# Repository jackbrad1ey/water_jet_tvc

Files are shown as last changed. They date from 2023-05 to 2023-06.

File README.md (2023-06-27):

Storage and collaboration repository for MEC2402 water jet TVC development.
The purpose of this project was to design and construct a vehicle capable of testing TVC control algorithms. Water is used as its method of propulsion to greatly reduce costs and time during development and ensure safety, allowing for rapid iteration and testing of new control algorithms.

The project features:
- Neptune, a custom flight computer designed to handle communication with ground station, control our servo motors, read from sensors and more.
- Neptune's firmware, consisting of a real time operating system that reads from our sensors and executes instructions based on packets sent from ground station.
- Ground station software, which is used to interact with the vehicle via a Jumper T-lite controller.
- CAD files for the vehicle and the associated testing stand.



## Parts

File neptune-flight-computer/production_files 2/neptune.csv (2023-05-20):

Comment | Designator | Footprint | LCSC
15p | C1,C2 | Capacitor_SMD:C_0805_2012Metric | C1562
10u | C12,C14 | Capacitor_SMD:C_0805_2012Metric_Pad1.18x1.45mm_HandSolder | C440198
1u | C13,C16,C20 | Capacitor_SMD:C_0402_1005Metric
8.2n | C15 | Capacitor_SMD:C_0402_1005Metric | C45186
1n | C17 | Capacitor_SMD:C_0402_1005Metric
10p | C18 | Capacitor_SMD:C_0402_1005Metric
10u | C19 | Capacitor_SMD:C_0603_1608Metric | C19702
10n | C22 | Capacitor_SMD:C_0603_1608Metric
1u | C23 | Capacitor_SMD:C_0603_1608Metric
4.7u | C26 | Capacitor_SMD:C_0603_1608Metric
33p | C3,C21 | Capacitor_SMD:C_0805_2012Metric
100nF | C4,C5,C6,C7,C8,C9,C10,C11,C24,C25 | Capacitor_SMD:C_0603_1608Metric
B5819W | D1,D3 | Diode_SMD:D_SOD-123 | C8598
RB056LAM-40TR | D2 | Diode_SMD:D_SMA | C308719
MountingHole | H1,H2,H3,H4 | MountingHole:MountingHole_3.2mm_M3
THD2528-11SD-GF | J1 | Local Library:THD252811SDGF
Conn_01x02 | J2 | Local Library:XT30PWM
Conn_Coaxial | J3 | Connector_Coaxial:SMA_Amphenol_132291_Vertical
USB_B_Micro | J4 | Connector_USB:USB_Micro-B_Molex-105017-0001
Conn_01x04 | J5,J6,J7 | Connector_PinHeader_2.54mm:PinHeader_1x04_P2.54mm_Vertical
IHLP2020CZER100M01 | L1 | Local Library:IHLP2020CZER100M01 | C844996
10u | L2 | Inductor_SMD:L_0805_2012Metric
Si2301-TP | Q1 | Package_TO_SOT_SMD:SOT-23 | C10487
AO3401A | Q2 | Package_TO_SOT_SMD:SOT-23 | C15127
56k | R1 | Resistor_SMD:R_0402_1005Metric
100k | R2,R5 | Resistor_SMD:R_0402_1005Metric
30k | R3 | Resistor_SMD:R_0402_1005Metric
10k | R4,R10,R11 | Resistor_SMD:R_0402_1005Metric
NC | R6 | Resistor_SMD:R_0402_1005Metric
36.5k | R7 | Resistor_SMD:R_0402_1005Metric | C162860
10.2k | R8 | Resistor_SMD:R_0603_1608Metric | C234238
1.91k | R9 | Resistor_SMD:R_0603_1608Metric | C217858
TS-1187A-B-A-B | SW1,SW2 | Button_Switch_SMD:SW_Push_1P1T_NO_CK_KSC6xxJ | C318884
ADR5040ARTZ-2.048 | U1 | Package_TO_SOT_SMD:SOT-23 | C144273
LM393 | U2 | Local Library:SOIC127P600X175-8N | C7955
TPS54331D | U3 | Package_SO:SOIC-8-1EP_3.9x4.9mm_P1.27mm_EP2.29x3mm_ThermalVias | C9865
LP3993-33B3F | U4 | Package_TO_SOT_SMD:SOT-23 | C387705
RFM95W-915S2 | U5 | RF_Module:HOPERF_RFM9XW_SMD
USBLC6-2SC6 | U6 | Package_TO_SOT_SMD:SOT-23-6 | C2827654
STM32F411RETx | U7 | Package_QFP:LQFP-64_10x10mm_P0.5mm | C94355
BMX055 | U8 | Local Library:BMX055
32.768k | Y1 | Crystal:Crystal_SMD_3215-2Pin_3.2x1.5mm | C620155
12MHz | Y2 | Crystal:Crystal_SMD_5032-4Pin_5.0x3.2mm

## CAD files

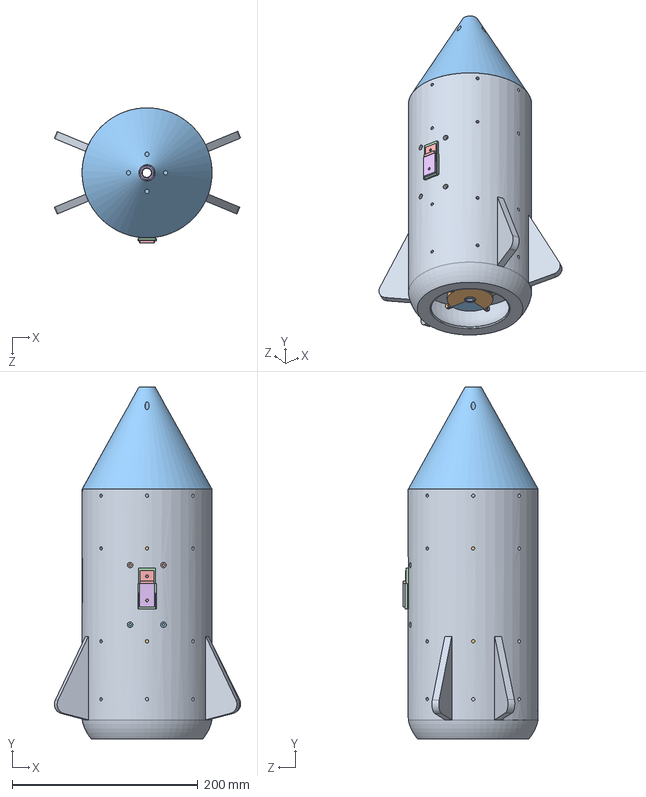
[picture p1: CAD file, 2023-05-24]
CAD/Vehicle_assembly.SLDASM
200.7 x 379.0 x 145.8 mm
Bodytube
2nozzleservorodmount - pt1
2nozzleservorodmount - pt2
v3-ballheadjoint x 2
v2-ballattatchemnet x 4
rods x 2
v3-ballheadjoint - servoside x 2
servo x 2
tvcbulkhead
Bottom half tube
Battery casing
PCB
Battery casing upper
Nozzle connection
nozzle-Pipe adapter
PVC pipe
step push fitting
Upper connection
nosecone
cable puller (sticks out less)
hinge placeholder
door

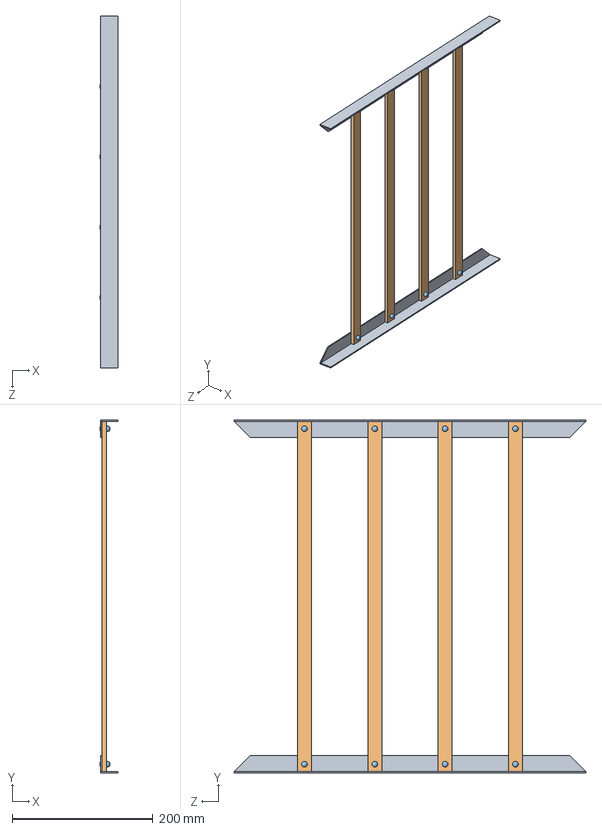
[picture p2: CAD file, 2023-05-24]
CAD/Cage/Roof.SLDASM
26.2 x 502.0 x 500.0 mm
right_angle x 2
Halfbar(roof) x 4
4mm rivet x 8

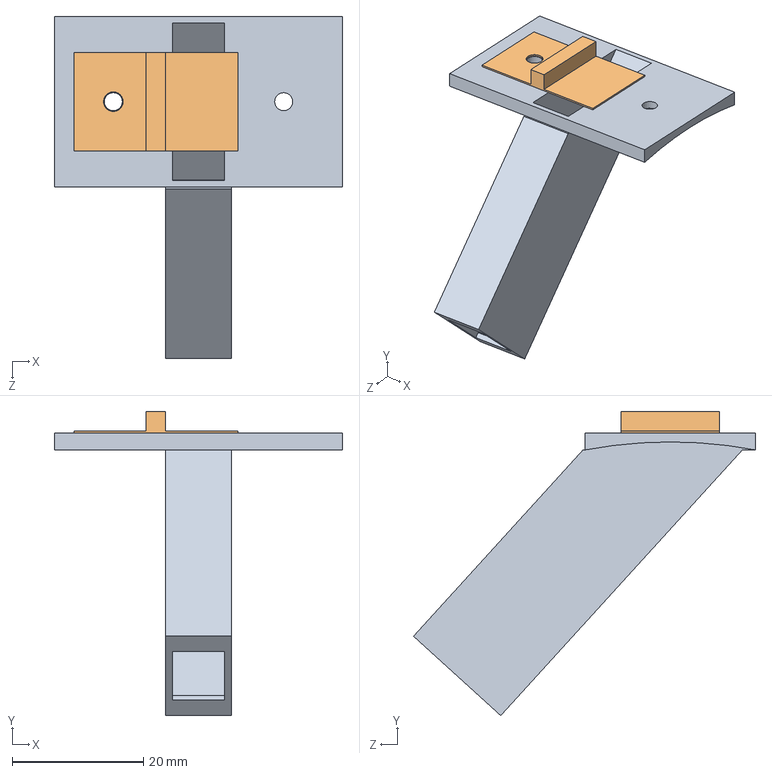
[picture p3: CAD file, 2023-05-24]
CAD/Sensor stack/puller.SLDASM
44.0 x 46.4 x 52.2 mm
cable puller (sticks out less)
hinge placeholder

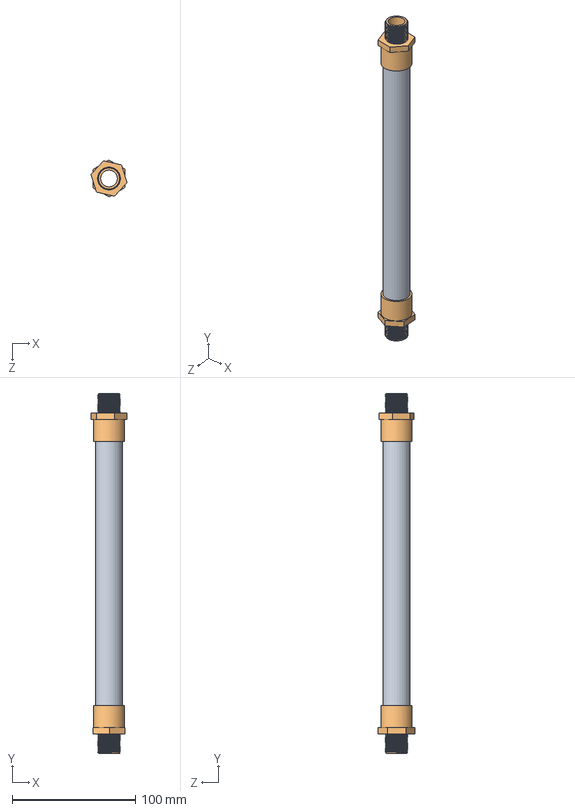
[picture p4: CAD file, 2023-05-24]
CAD/Water Delivery/Plenum pipe assem.SLDASM
29.3 x 292.0 x 30.0 mm
PVC pipe_2.0
0.5_inch_male x 2

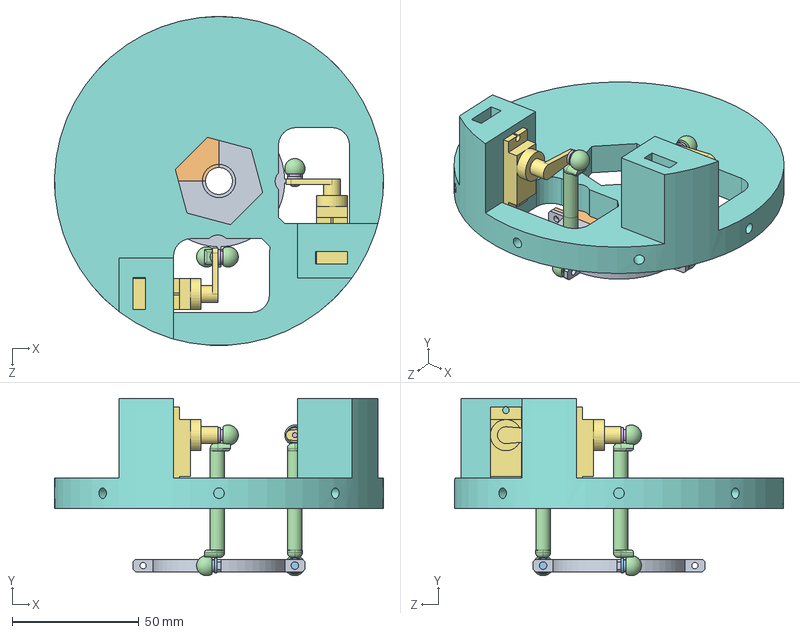
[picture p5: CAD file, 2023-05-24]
CAD/TVC/tvc_assem.SLDASM
130.0 x 70.1 x 130.0 mm
2nozzleservorodmount - pt1
2nozzleservorodmount - pt2
v3-ballheadjoint x 2
v2-ballattatchemnet x 4
rods x 2
v3-ballheadjoint - servoside x 2
servo x 2
tvcbulkhead

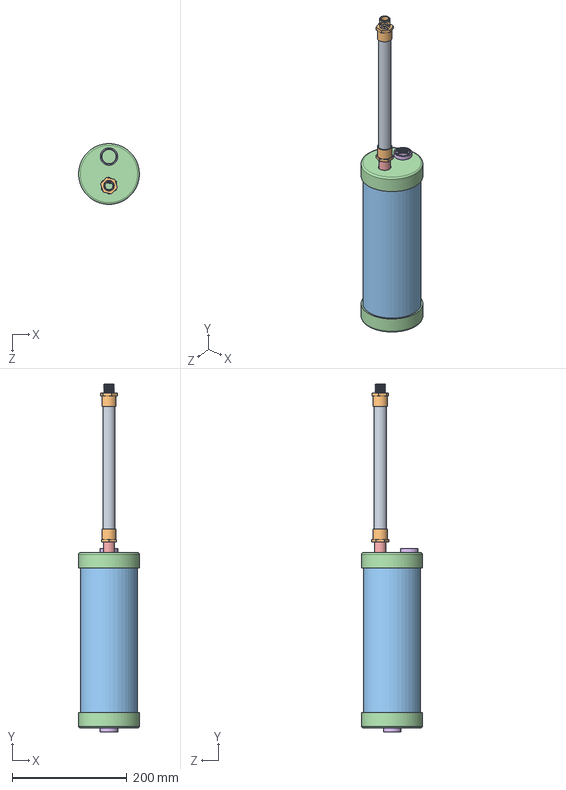
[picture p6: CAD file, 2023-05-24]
CAD/Water Delivery/Plenum full assem.SLDASM
106.0 x 607.0 x 106.0 mm
PVC pipe_2.0
0.5_inch_male x 2
Plenum_pipe
plenum_end_cap x 2
0.5_inch_female
female_3.4_inch x 2

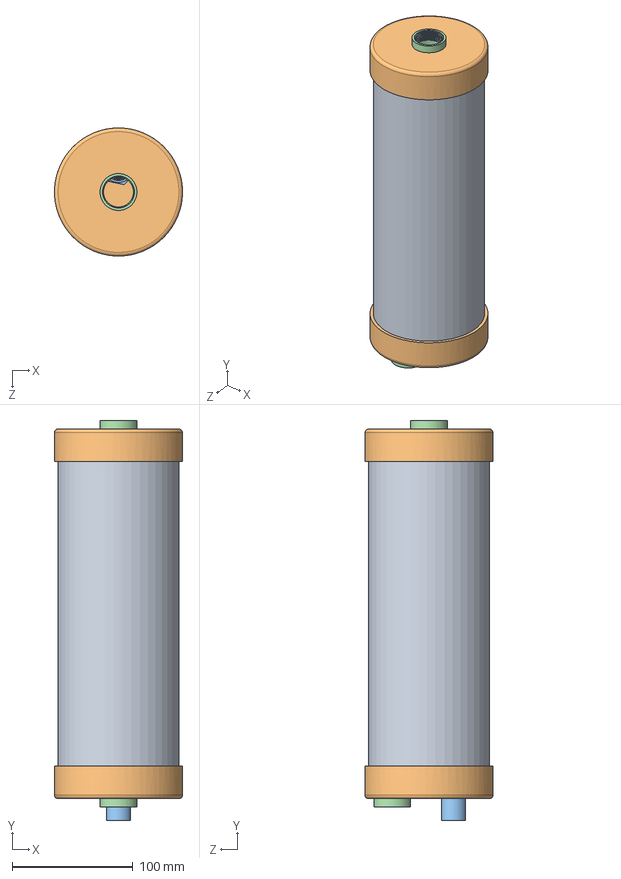
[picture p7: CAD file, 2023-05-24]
CAD/Water Delivery/plenum.SLDASM
106.0 x 331.0 x 106.0 mm
Plenum_pipe
plenum_end_cap x 2
0.5_inch_female
female_3.4_inch x 2

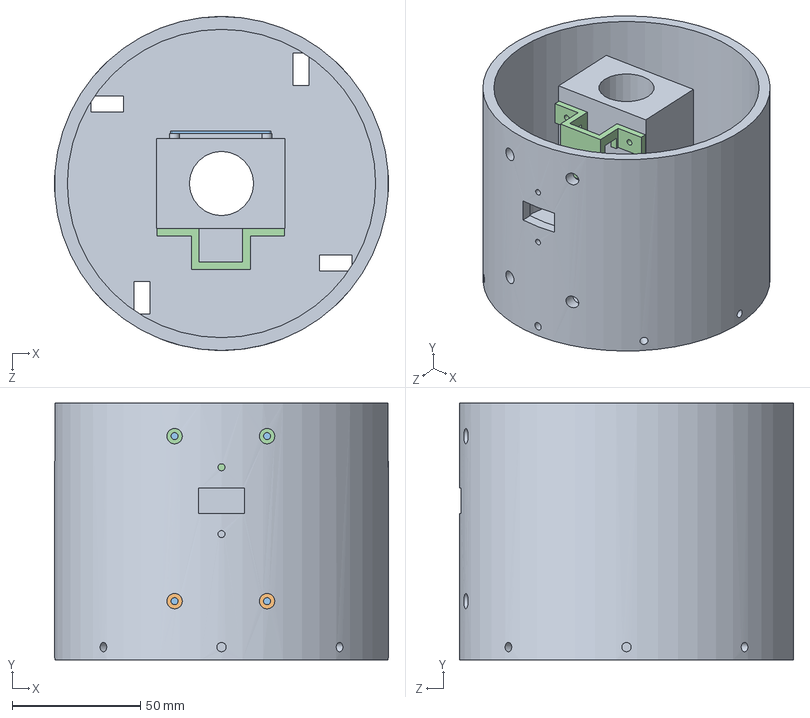
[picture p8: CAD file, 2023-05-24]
CAD/Sensor stack/sensor stack assem.SLDASM
130.0 x 100.0 x 130.0 mm
Bottom half tube
Battery casing
PCB
Battery casing upper

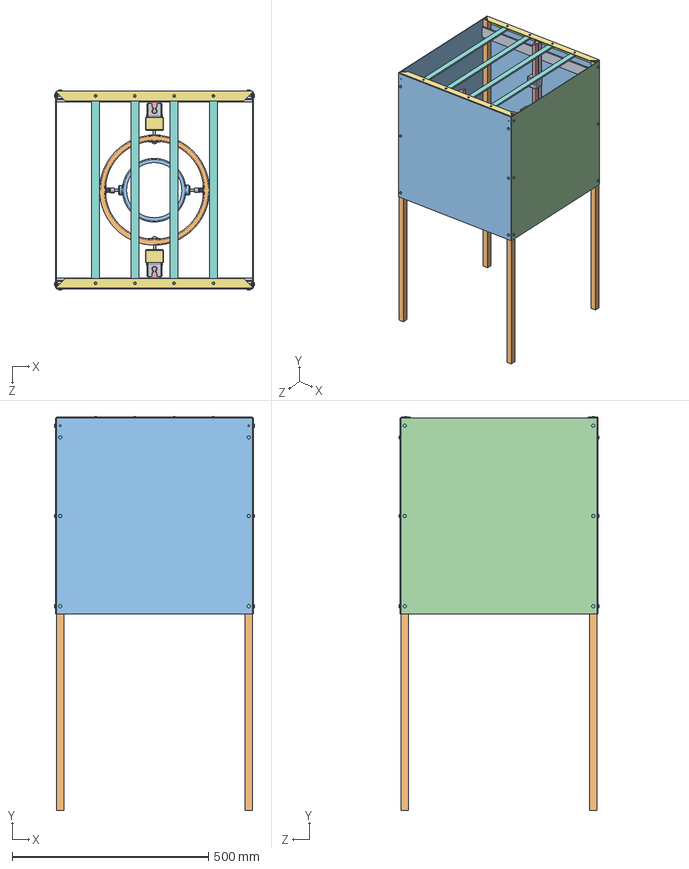
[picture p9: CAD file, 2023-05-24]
CAD/Cage/Cage.SLDASM
510.0 x 1003.2 x 510.0 mm
Bar x 4
RotationRing
InnerRotationMount
BoltSquare x 4
22x8x7 bearing x 4
RingHardstop x 2
right_angle x 2
Halfbar(roof) x 4
4mm rivet x 8
SHS x 4
Polycarbonate Sheet x 3
Plywood Sheet
SBR12 Linear Rail x 2
SBR12UU x 2
SBR12UU Mount x 2
m5 bolt_unthreaded x 24
Hardstop x 4

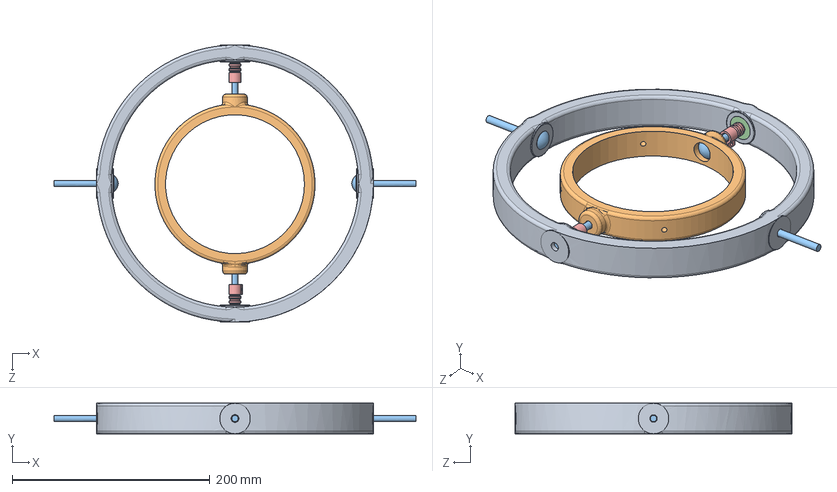
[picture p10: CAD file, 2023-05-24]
CAD/Cage/CageAssembly.SLDASM
366.0 x 31.0 x 280.0 mm
RotationRing
InnerRotationMount
BoltSquare x 4
22x8x7 bearing x 2
RingHardstop x 2

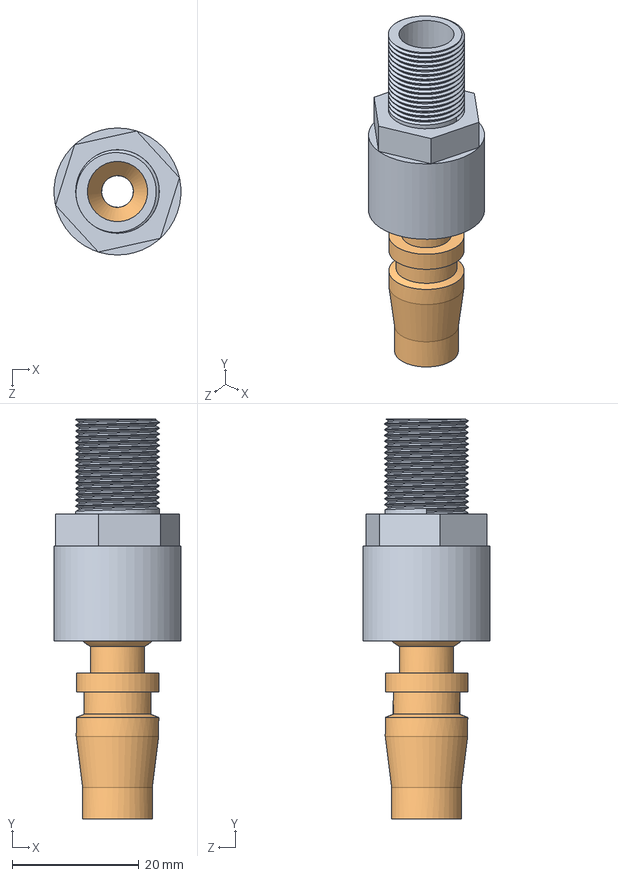
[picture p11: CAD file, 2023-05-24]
CAD/Water Delivery/Nozzle.SLDASM
20.0 x 63.0 x 20.0 mm
Nozzle top
NozzleTip

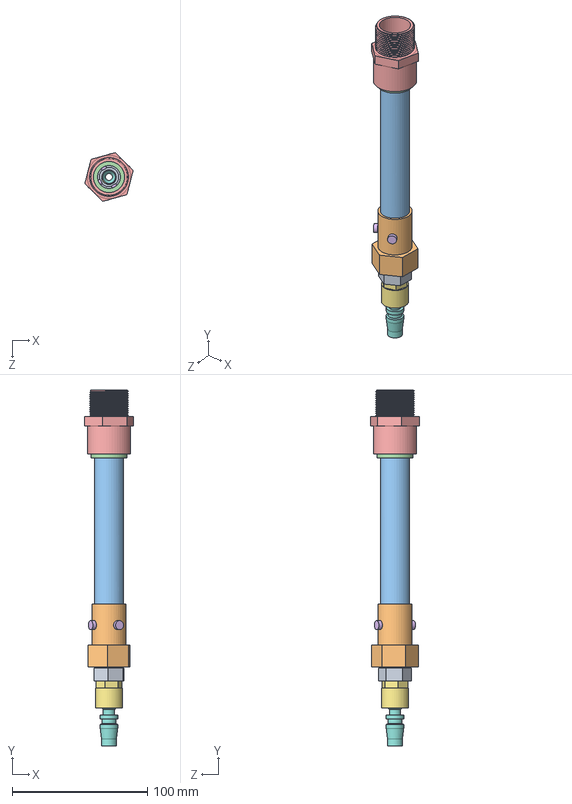
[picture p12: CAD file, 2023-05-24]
CAD/Water Delivery/Water Delivery.SLDASM
35.9 x 263.0 x 36.0 mm
Poly Threaded Bushing
Press faucet Socket
PVC pipe
Reducing Bushing
Press valve Socket
M4x6 bolt x 3
Nozzle top
NozzleTip

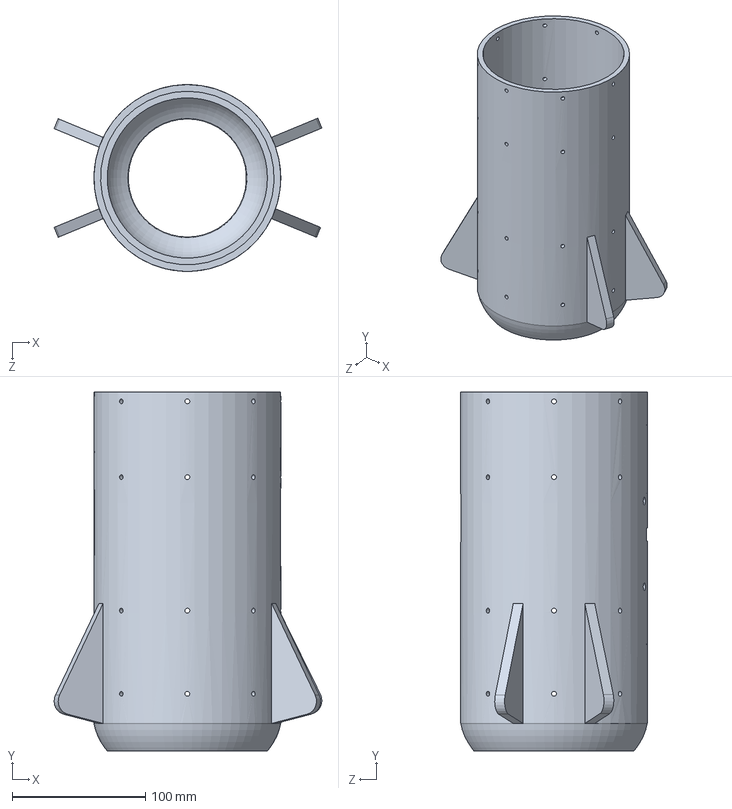
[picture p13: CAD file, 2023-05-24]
CAD/BODY/Bodytube.SLDPRT
200.7 x 269.0 x 140.0 mm

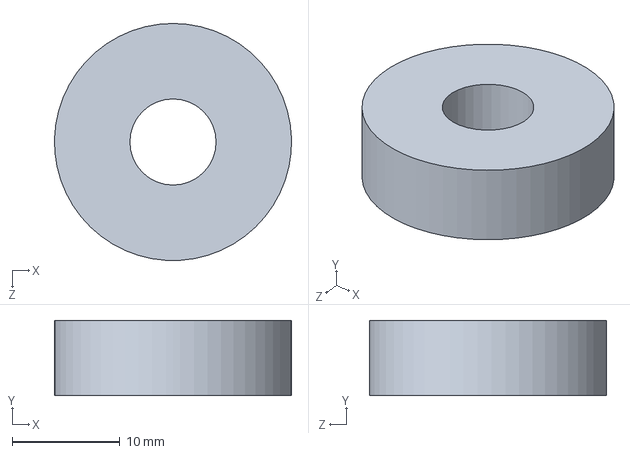
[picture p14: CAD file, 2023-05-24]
CAD/Cage/22x8x7 bearing.SLDPRT
22.0 x 7.00 x 22.0 mm

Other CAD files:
CAD/Sensor stack/PCB.SLDPRT
CAD/TVC/STLs/tvcbulkhead3.STL
CAD/TVC/v3-ballheadjoint - servoside.SLDPRT
CAD/BODY/nosecone.SLDPRT
CAD/BODY/STLs/Bodytube.STL
CAD/BODY/STLs/nosecone.STL
CAD/Cage/4.x.x/4.1.x/4.1.1.SLDDRW
CAD/Cage/4.x.x/4.1.x/4.1.2.SLDDRW
CAD/Cage/4.x.x/4.1.x/4.1.3.SLDDRW
CAD/Cage/4.x.x/4.1.x/4.1.4.SLDDRW
CAD/Cage/4.x.x/4.1.x/4.1.5.SLDDRW
CAD/Cage/4.x.x/4.1.x/4.1.6.SLDDRW
CAD/Cage/4.x.x/4.2.x/4.2.0.SLDDRW
CAD/Cage/4.x.x/4.2.x/4.2.1.SLDDRW
CAD/Cage/4.x.x/4.2.x/4.2.2.SLDDRW
CAD/Cage/4.x.x/4.2.x/4.2.3.SLDDRW
CAD/Cage/4.x.x/4.3.x/4.3.0.SLDDRW
CAD/Cage/4.x.x/4.3.x/4.3.1.SLDDRW
CAD/Cage/4.x.x/4.3.x/4.3.2.SLDDRW
CAD/Cage/4mm rivet.SLDPRT
CAD/Cage/Bar.SLDPRT
CAD/Cage/BoltSquare.SLDPRT
CAD/Cage/Halfbar(roof).SLDPRT
CAD/Cage/Hardstop.SLDPRT
CAD/Cage/InnerRotationMount.SLDPRT
CAD/Cage/Plywood Sheet.SLDPRT
CAD/Cage/Polycarbonate Sheet.SLDPRT
CAD/Cage/RingHardstop.SLDPRT
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

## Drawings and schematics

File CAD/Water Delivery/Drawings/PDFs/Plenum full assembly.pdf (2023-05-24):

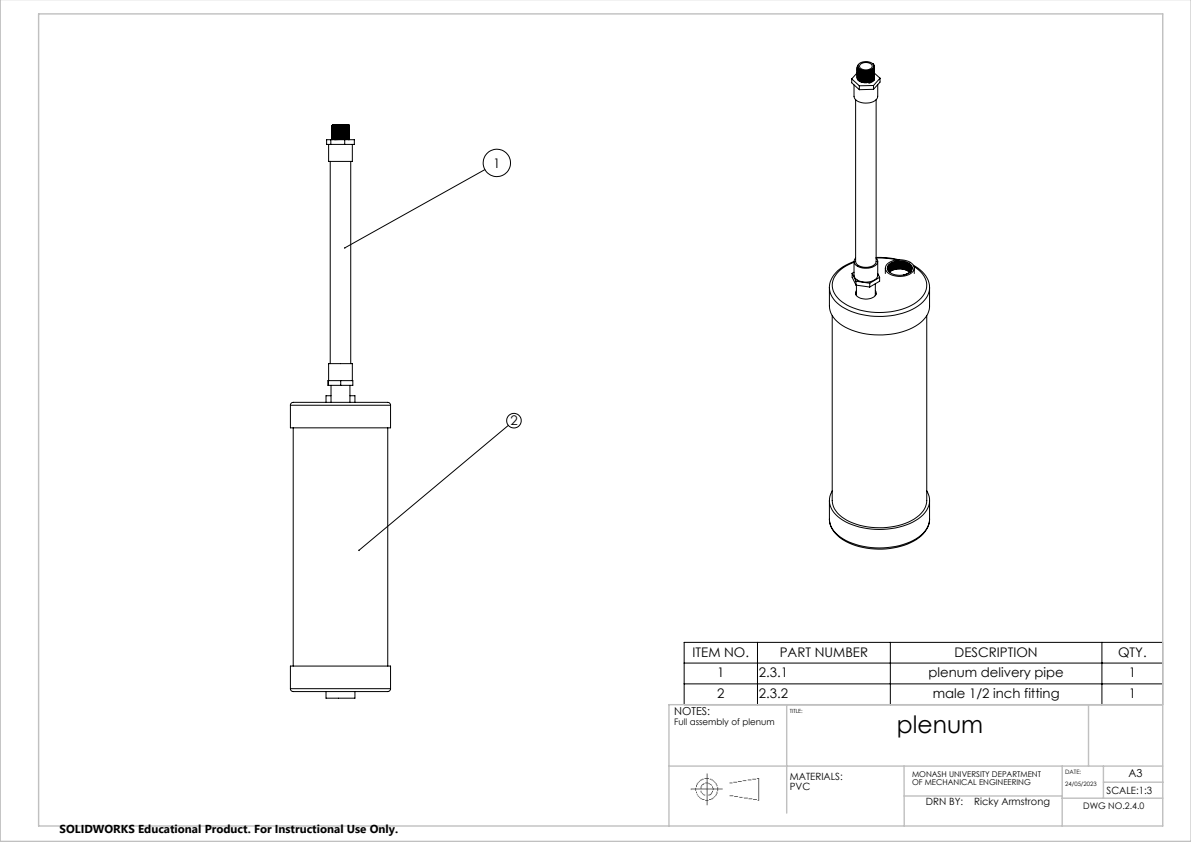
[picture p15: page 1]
DWG NO.2.4.0

ITEM NO. | PART NUMBER | DESCRIPTION | QTY.
1 | 2.3.1 | plenum delivery pipe | 1
2 | 2.3.2 | male 1/2 inch fitting | 1
NOTES: Full assembly of plenum | TITLE: plenum

MONASH UNIVERSITY DEPARTMENT OF MECHANICAL ENGINEERING | DATE: 24/05/2023 | A3

DRN BY: Ricky Armstrong

SOLIDWORKS Educational Product. For Instructional Use Only.

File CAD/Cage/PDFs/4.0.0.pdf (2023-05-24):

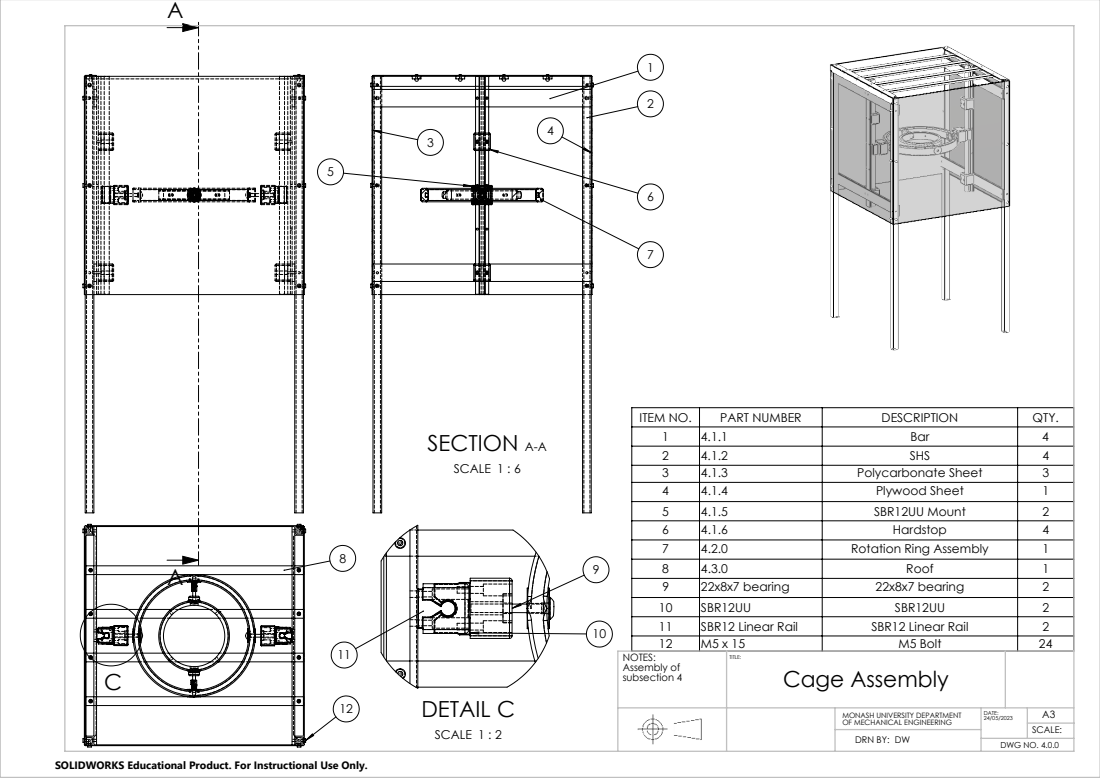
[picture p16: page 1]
SECTION A-A; SCALE 1 : 6; DETAIL C; SCALE 1 : 2; ITEM NO.; PART NUMBER; DESCRIPTION; QTY.; Polycarbonate Sheet; Plywood Sheet; SBR12UU Mount; Rotation Ring Assembly; 22x8x7 bearing; SBR12 Linear Rail; M5 Bolt; DWG NO. 4.0.0; Cage Assembly; Assembly of subsection 4

MONASH UNIVERSITY DEPARTMENT
OF MECHANICAL ENGINEERING
DRN BY: DW

SOLIDWORKS Educational Product. For Instructional Use Only.

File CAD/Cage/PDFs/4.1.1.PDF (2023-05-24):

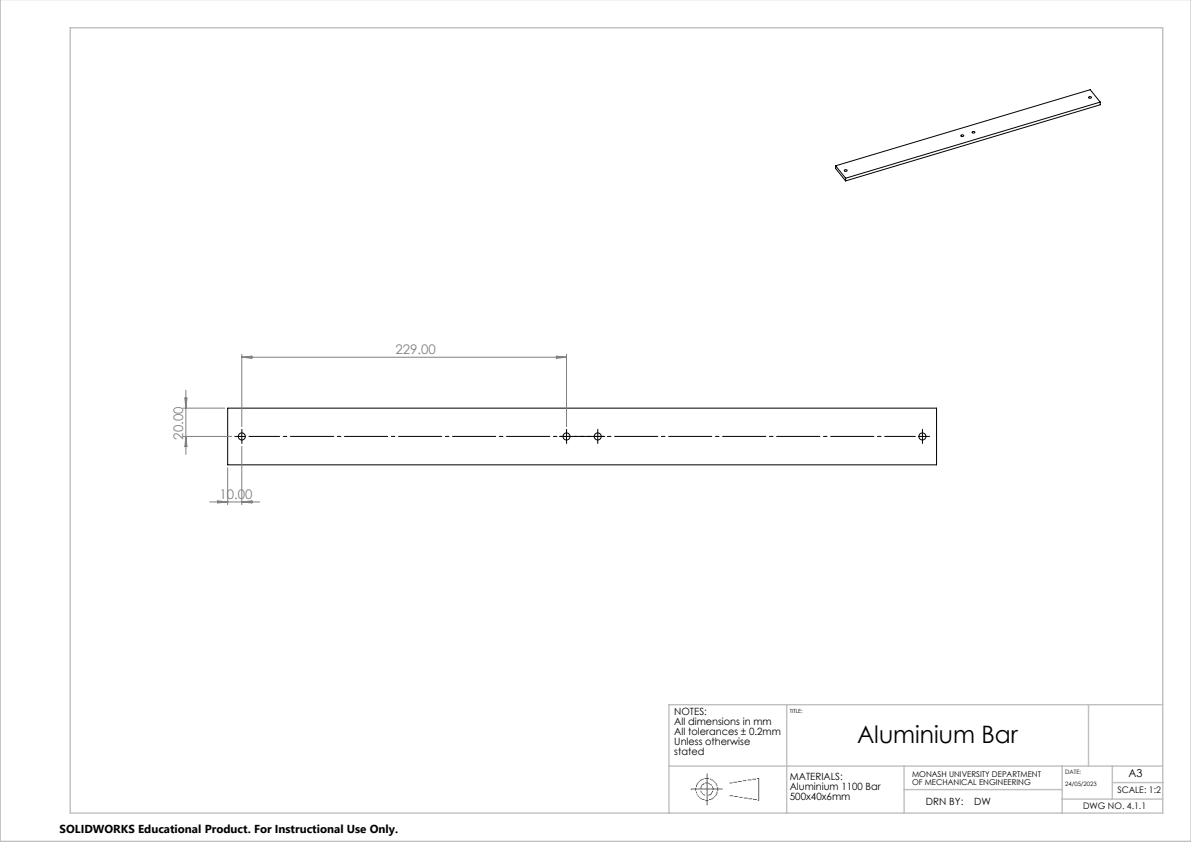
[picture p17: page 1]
DWG NO. 4.1.1; SCALE: 1:2

NOTES: All dimensions in mm All tolerances ± 0.2mm Unless otherwise stated | TITLE: Aluminium Bar

MATERIALS: Aluminium 1100 Bar 500x40x6mm | MONASH UNIVERSITY DEPARTMENT OF MECHANICAL ENGINEERING | DATE: 24/05/2023 | A3

DRN BY: DW

SOLIDWORKS Educational Product. For Instructional Use Only.

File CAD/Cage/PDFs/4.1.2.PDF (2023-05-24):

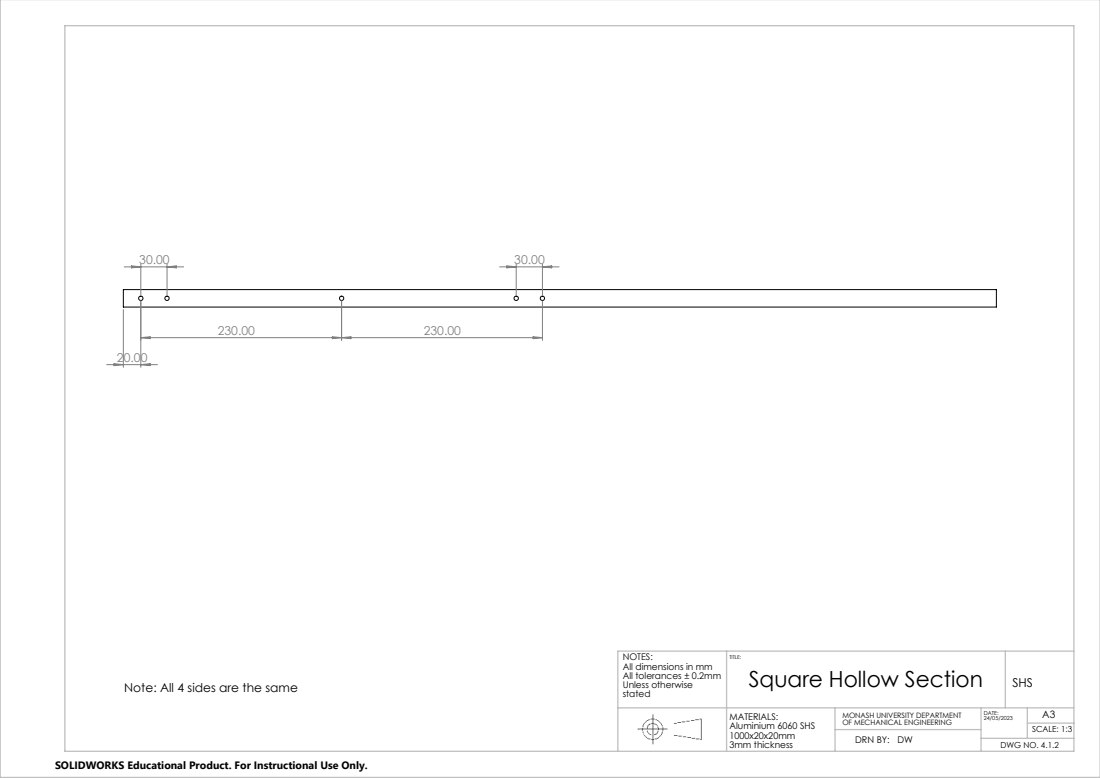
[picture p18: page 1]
DWG NO. 4.1.2; SCALE: 1:3

NOTES: All dimensions in mm All tolerances ± 0.2mm Unless otherwise stated | TITLE: Square Hollow Section | SHS

Note: All 4 sides are the same

MATERIALS: Aluminium 6060 SHS 1000x20x20mm 3mm thickness | MONASH UNIVERSITY DEPARTMENT OF MECHANICAL ENGINEERING | DATE: 24/05/2023 | A3

DRN BY: DW

SOLIDWORKS Educational Product. For Instructional Use Only.

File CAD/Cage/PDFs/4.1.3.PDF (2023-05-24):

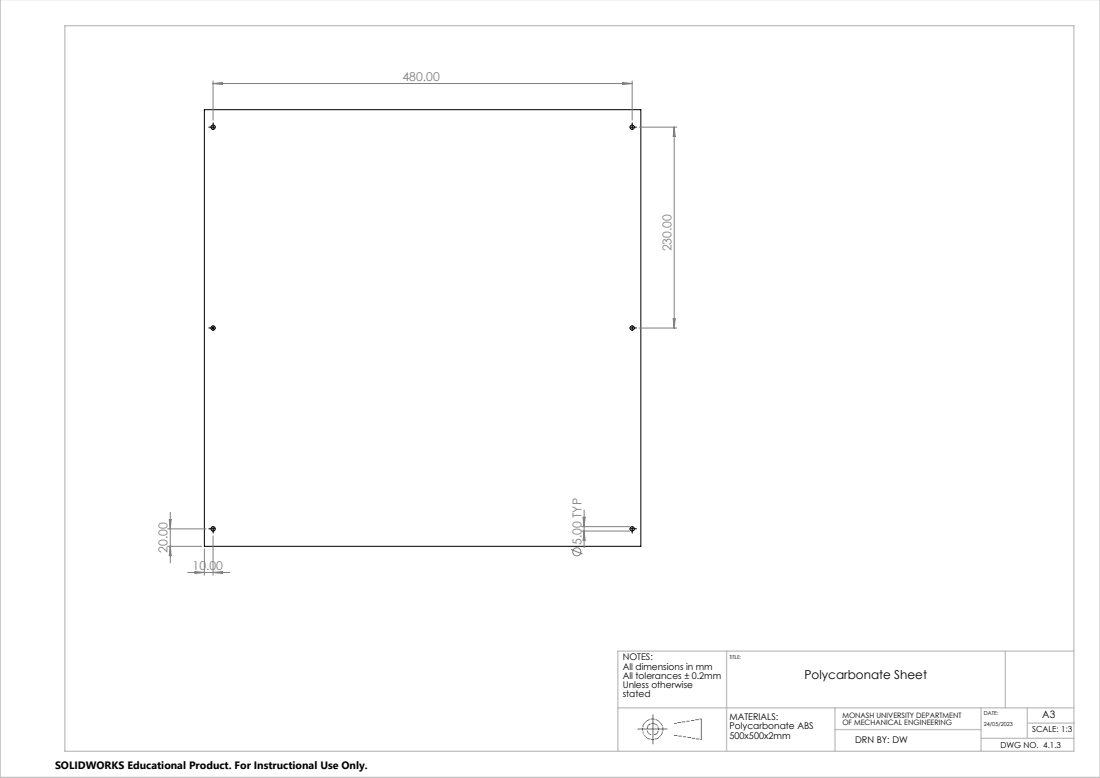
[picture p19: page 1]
5.00 TYP; DWG NO. 4.1.3; SCALE: 1:3

NOTES: All dimensions in mm All tolerances ± 0.2mm Unless otherwise stated | TITLE: Polycarbonate Sheet

MATERIALS: Polycarbonate ABS 500x500x2mm | MONASH UNIVERSITY DEPARTMENT OF MECHANICAL ENGINEERING | DATE: 24/05/2023 | A3

DRN BY: DW

SOLIDWORKS Educational Product. For Instructional Use Only.

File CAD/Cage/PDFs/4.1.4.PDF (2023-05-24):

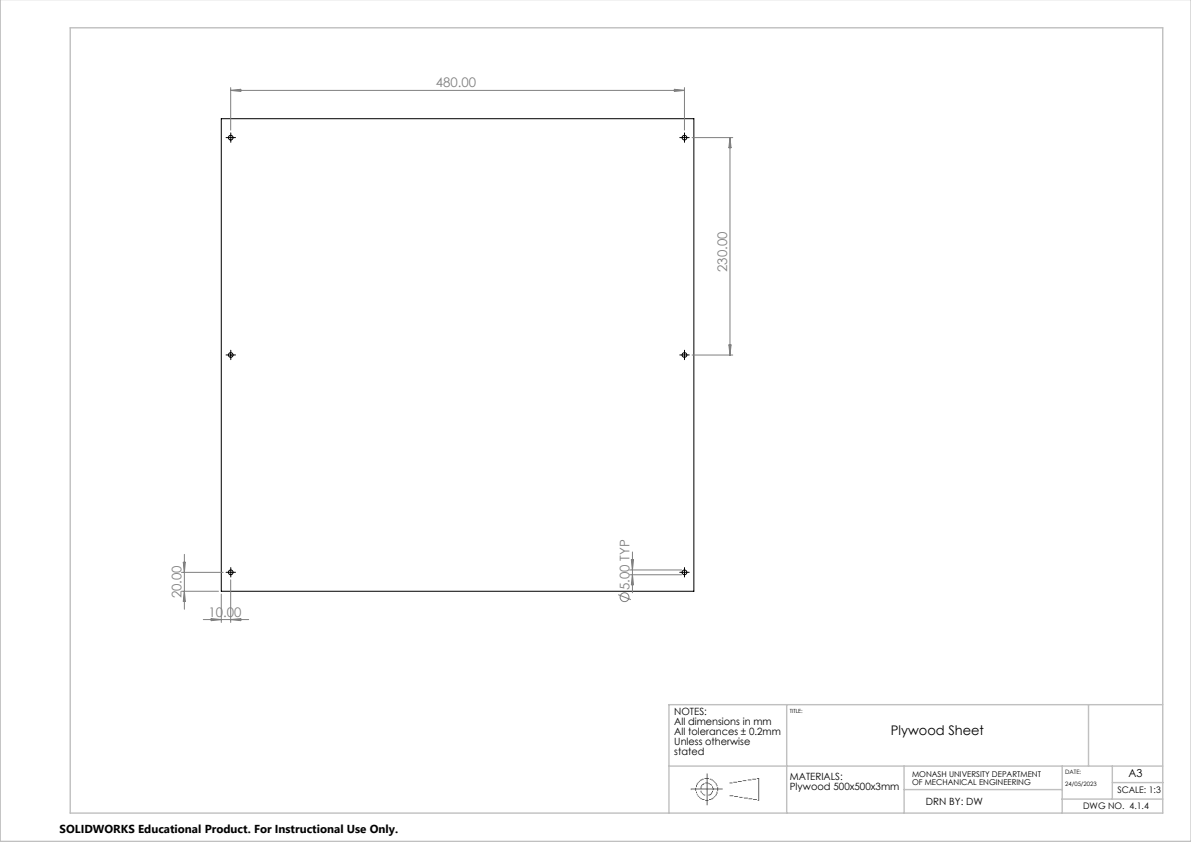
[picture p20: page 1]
5.00 TYP; DWG NO. 4.1.4; SCALE: 1:3

NOTES: All dimensions in mm All tolerances ± 0.2mm Unless otherwise stated | TITLE: Plywood Sheet

MATERIALS: Plywood 500x500x3mm | MONASH UNIVERSITY DEPARTMENT OF MECHANICAL ENGINEERING | DATE: 24/05/2023 | A3

DRN BY: DW

SOLIDWORKS Educational Product. For Instructional Use Only.

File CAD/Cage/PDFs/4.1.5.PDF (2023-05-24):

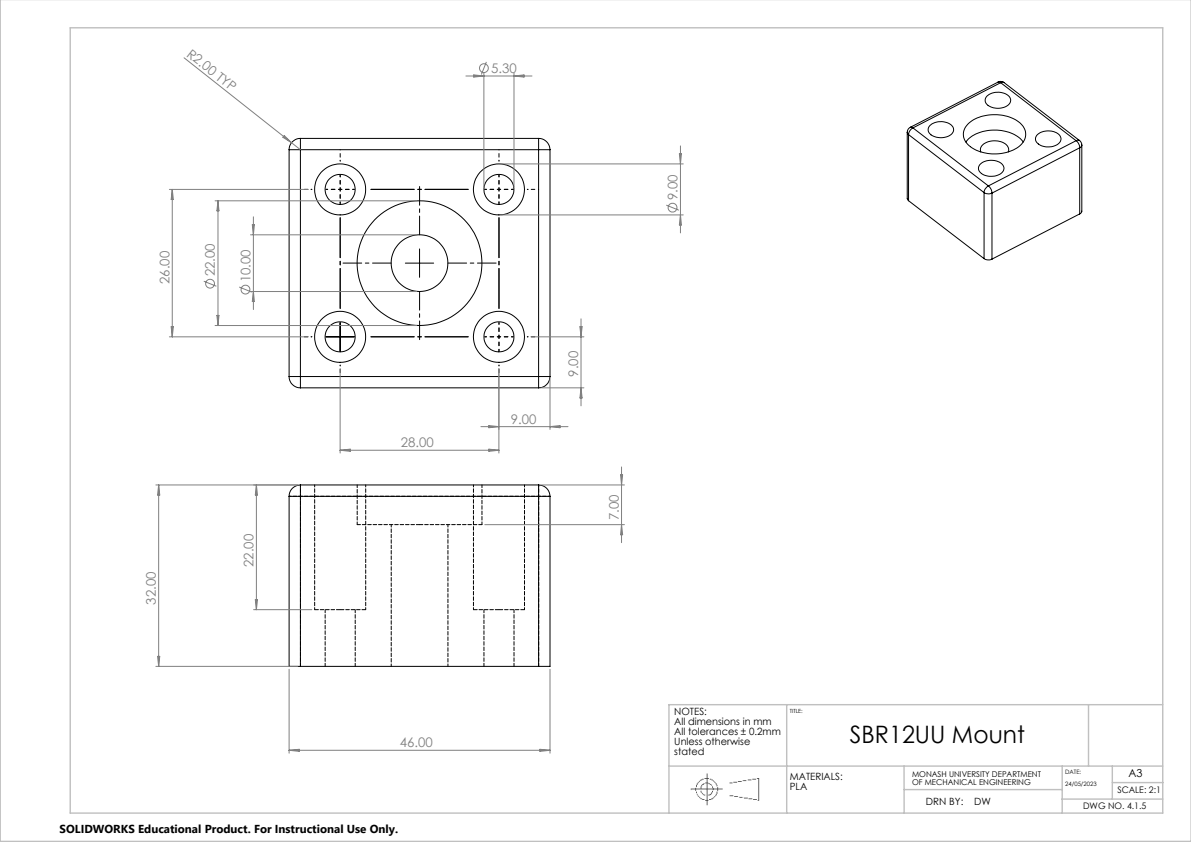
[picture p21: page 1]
R2.00 TYP; DWG NO. 4.1.5; SCALE: 2:1

NOTES: All dimensions in mm All tolerances ± 0.2mm Unless otherwise stated | TITLE: SBR12UU Mount

MATERIALS: PLA | MONASH UNIVERSITY DEPARTMENT OF MECHANICAL ENGINEERING | DATE: 24/05/2023 | A3

DRN BY: DW

SOLIDWORKS Educational Product. For Instructional Use Only.

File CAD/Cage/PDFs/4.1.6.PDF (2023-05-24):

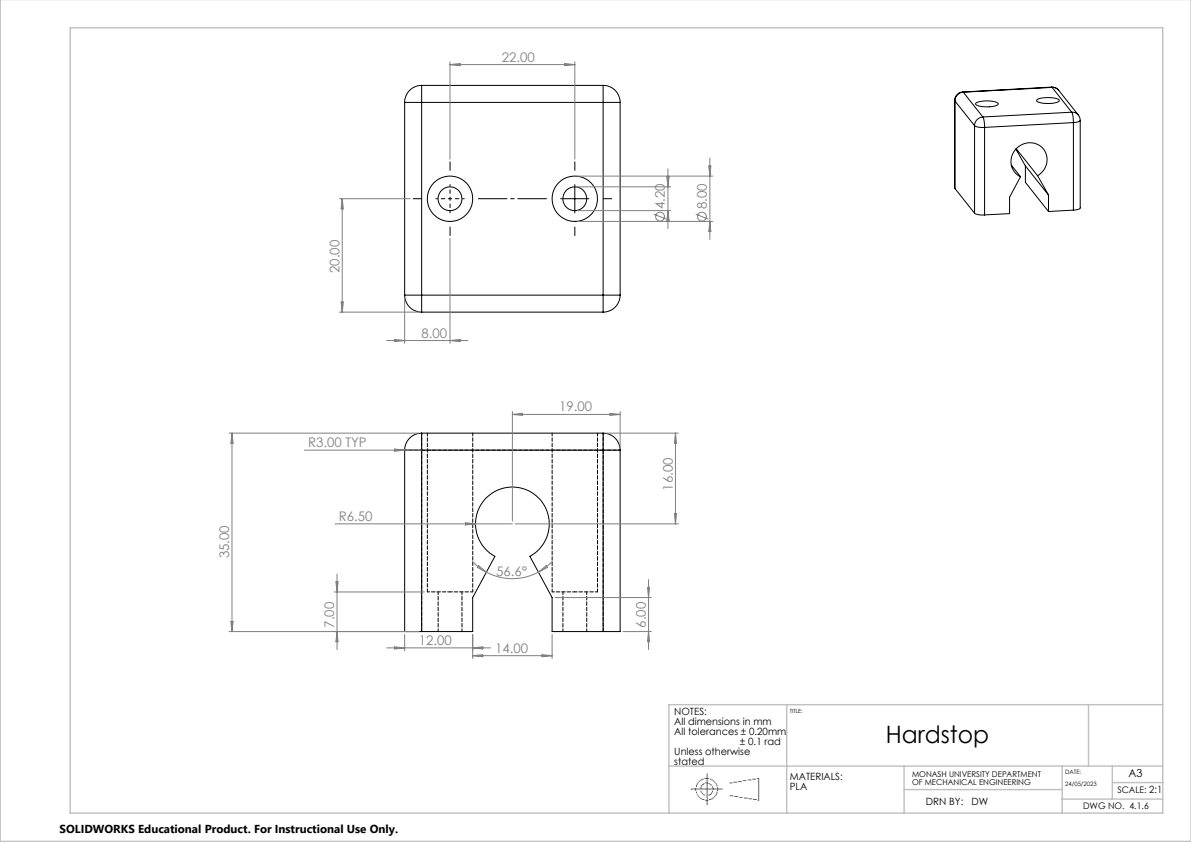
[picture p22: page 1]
R3.00 TYP; DWG NO. 4.1.6; SCALE: 2:1

NOTES: All dimensions in mm All tolerances ± 0.20mm ± 0.1 rad Unless otherwise stated | TITLE: Hardstop

MATERIALS: PLA | MONASH UNIVERSITY DEPARTMENT OF MECHANICAL ENGINEERING | DATE: 24/05/2023 | A3

DRN BY: DW

SOLIDWORKS Educational Product. For Instructional Use Only.

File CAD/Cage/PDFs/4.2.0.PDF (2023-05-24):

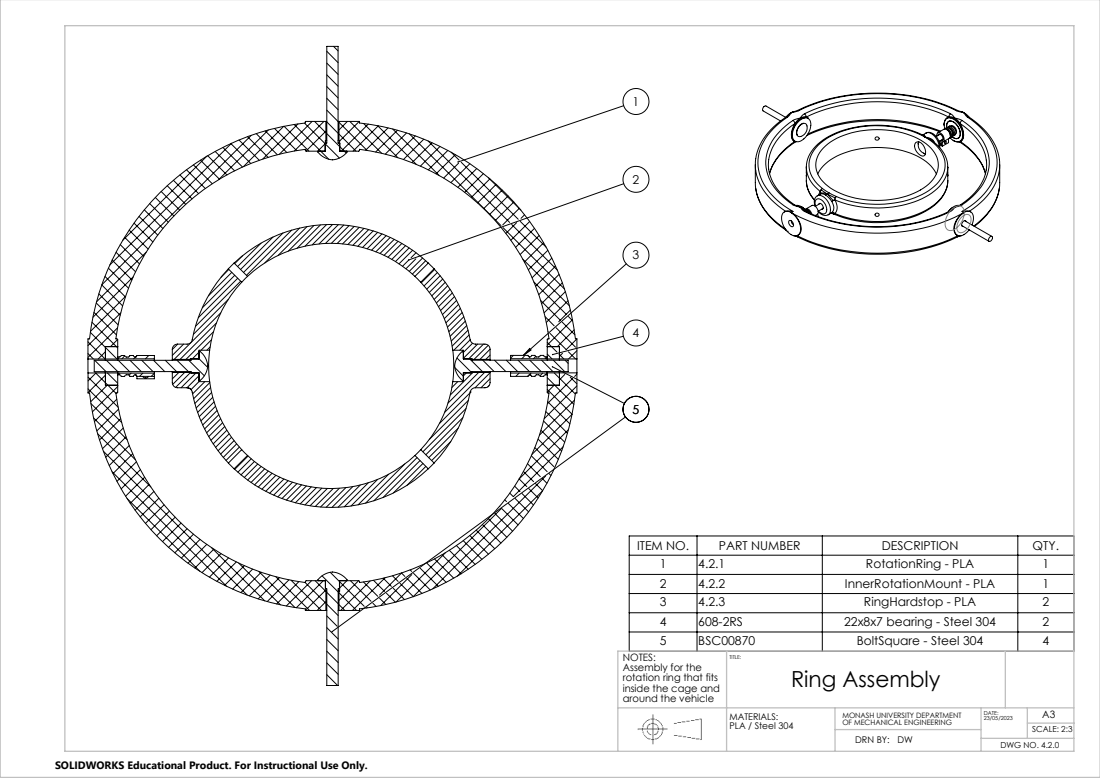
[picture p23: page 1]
DWG NO. 4.2.0; SCALE: 2:3

ITEM NO. | PART NUMBER | DESCRIPTION | QTY.
1 | 4.2.1 | RotationRing - PLA | 1
2 | 4.2.2 | InnerRotationMount - PLA | 1
3 | 4.2.3 | RingHardstop - PLA | 2
4 | 608-2RS | 22x8x7 bearing - Steel 304 | 2
5 | BSC00870 | BoltSquare - Steel 304 | 4
NOTES: Assembly for the rotation ring that fits inside the cage and around the vehicle | TITLE: Ring Assembly

MATERIALS: PLA / Steel 304 | MONASH UNIVERSITY DEPARTMENT OF MECHANICAL ENGINEERING | DATE: 23/05/2023 | A3

DRN BY: DW

SOLIDWORKS Educational Product. For Instructional Use Only.

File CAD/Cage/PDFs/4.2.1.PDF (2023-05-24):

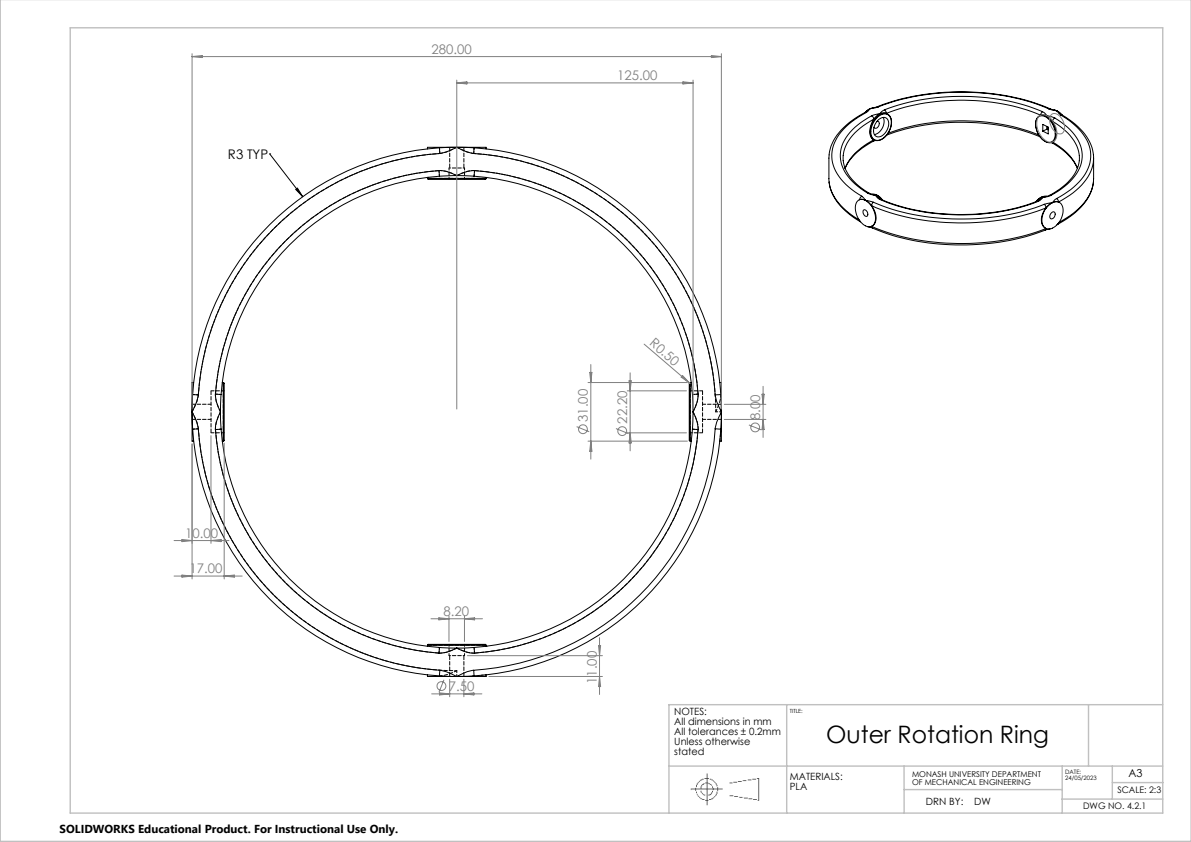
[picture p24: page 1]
R3 TYP; DWG NO. 4.2.1; SCALE: 2:3

NOTES: All dimensions in mm All tolerances ± 0.2mm Unless otherwise stated | TITLE: Outer Rotation Ring

MATERIALS: PLA | MONASH UNIVERSITY DEPARTMENT OF MECHANICAL ENGINEERING | DATE: 24/05/2023 | A3

DRN BY: DW

SOLIDWORKS Educational Product. For Instructional Use Only.

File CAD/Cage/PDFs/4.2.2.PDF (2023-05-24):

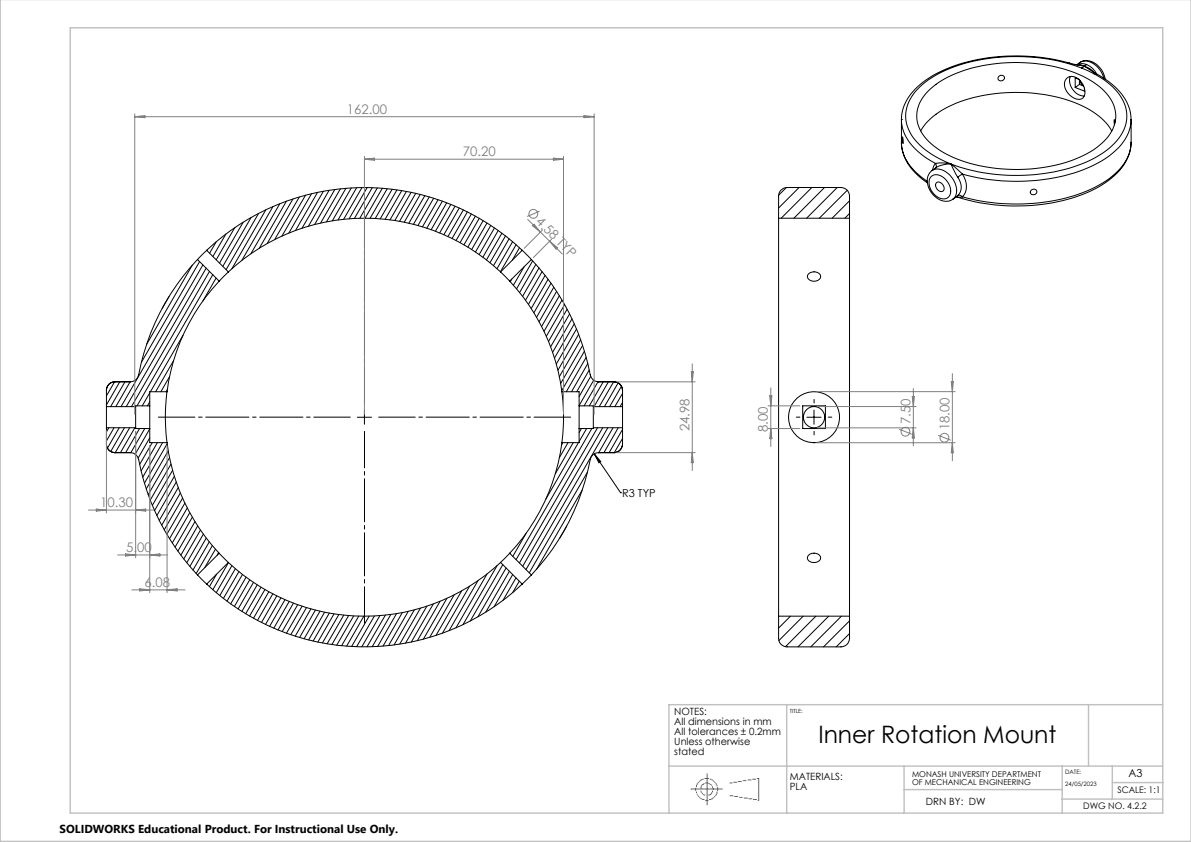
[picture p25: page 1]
4.58 TYP; R3 TYP; DWG NO. 4.2.2; SCALE: 1:1

NOTES: All dimensions in mm All tolerances ± 0.2mm Unless otherwise stated | TITLE: Inner Rotation Mount

MATERIALS: PLA | MONASH UNIVERSITY DEPARTMENT OF MECHANICAL ENGINEERING | DATE: 24/05/2023 | A3

DRN BY: DW

SOLIDWORKS Educational Product. For Instructional Use Only.

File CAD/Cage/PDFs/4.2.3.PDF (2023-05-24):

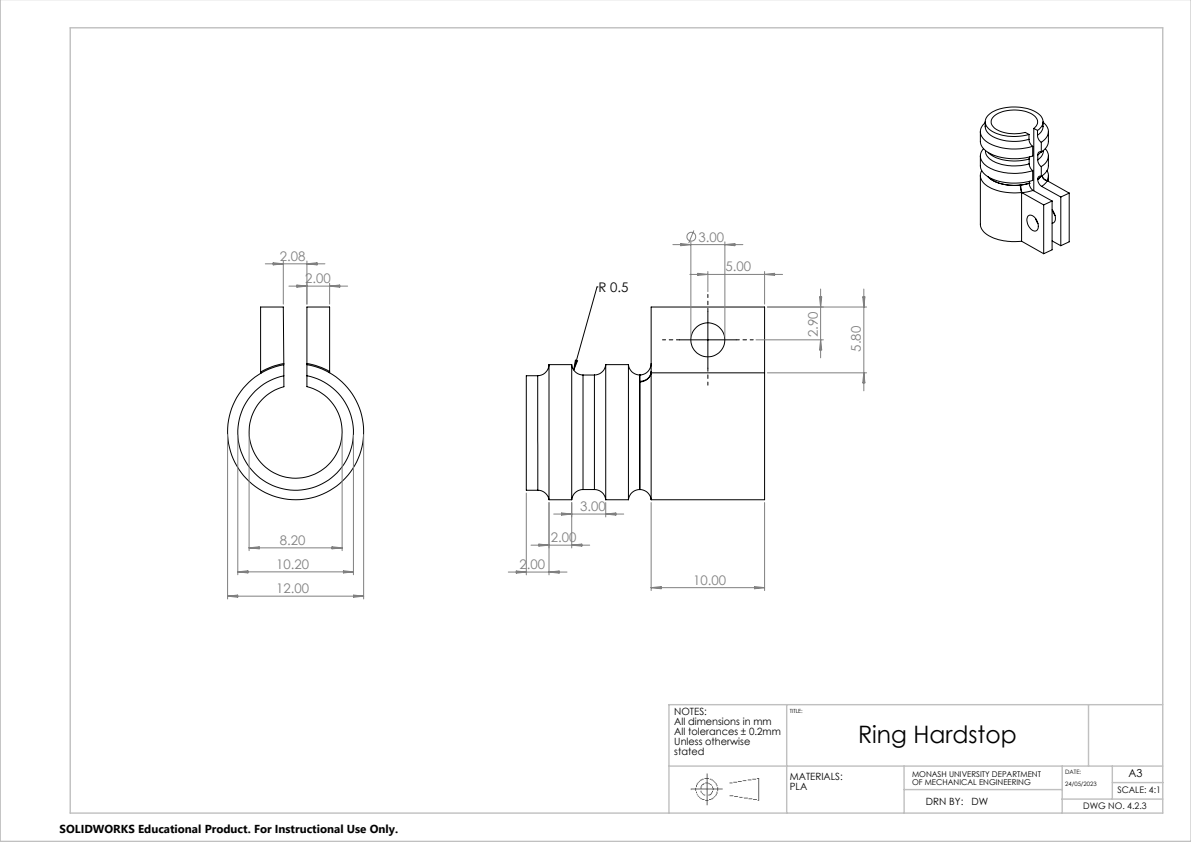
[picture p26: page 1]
DWG NO. 4.2.3; SCALE: 4:1

NOTES: All dimensions in mm All tolerances ± 0.2mm Unless otherwise stated | TITLE: Ring Hardstop

MATERIALS: PLA | MONASH UNIVERSITY DEPARTMENT OF MECHANICAL ENGINEERING | DATE: 24/05/2023 | A3

DRN BY: DW

SOLIDWORKS Educational Product. For Instructional Use Only.

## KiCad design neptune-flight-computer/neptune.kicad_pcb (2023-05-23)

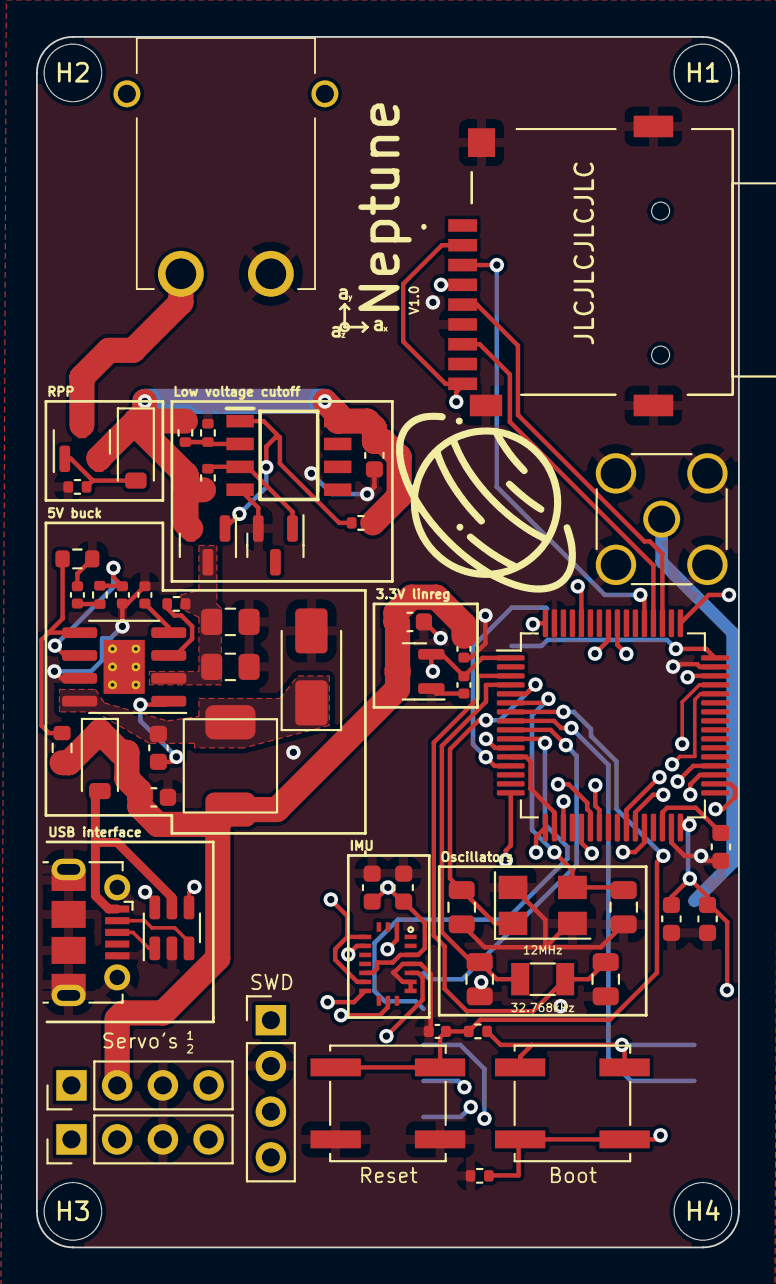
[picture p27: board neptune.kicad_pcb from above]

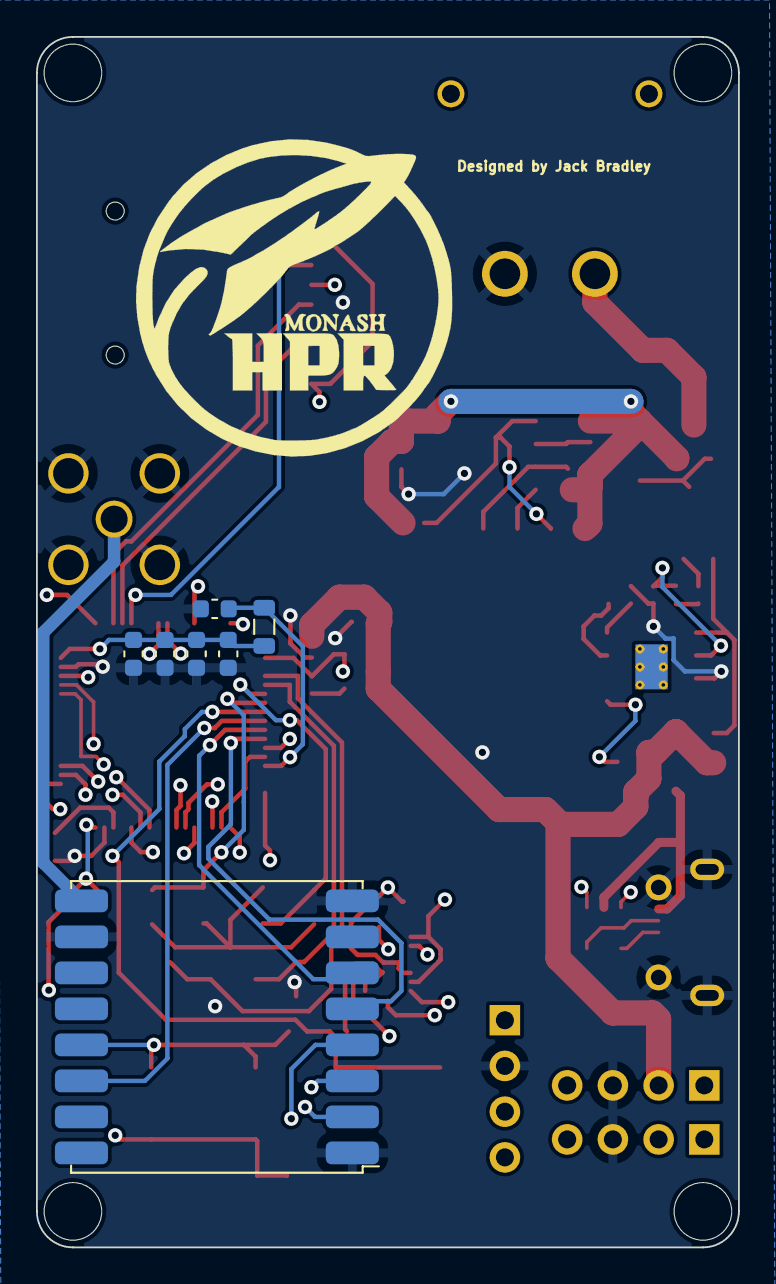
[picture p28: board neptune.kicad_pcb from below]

Board: 4 copper layers, 39.0 x 67.2 mm, 68 parts (8 on the bottom side), 54 nets.

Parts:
C1, C2: 15p; C_0805_2012Metric
C3, C21: 33p; C_0805_2012Metric
C4, C5, C6, C7, C8, C9, C10, C11, C24, C25: 100nF; C_0603_1608Metric
C12, C14: 10u; C_0805_2012Metric_Pad1.18x1.45mm_HandSolder
C13, C16, C20: 1u; C_0402_1005Metric
C15: 8.2n; C_0402_1005Metric
C17: 1n; C_0402_1005Metric
C18: 10p; C_0402_1005Metric
C19: 10u; C_0603_1608Metric
C22: 10n; C_0603_1608Metric
C23: 1u; C_0603_1608Metric
C26: 4.7u; C_0603_1608Metric
D1, D3: B5819W; D_SOD-123
D2: RB056LAM-40TR; D_SMA
H1, H2, H3, H4: MountingHole; MountingHole_3.2mm_M3
H5: HPR_Logo
J1: THD2528-11SD-GF; THD252811SDGF
J2: Conn_01x02; XT30PWM
J3: Conn_Coaxial; SMA_Amphenol_132291_Vertical
J4: USB_B_Micro; USB_Micro-B_Molex-105017-0001
J5, J6, J7: Conn_01x04; PinHeader_1x04_P2.54mm_Vertical
L1: IHLP2020CZER100M01
L2: 10u; L_0805_2012Metric
Q1: Si2301-TP; SOT-23
Q2: AO3401A; SOT-23
R1, R4: 30k; R_0402_1005Metric
R2, R5: 100k; R_0402_1005Metric
R3: 56k; R_0402_1005Metric
R6: NC; R_0402_1005Metric
R7: 36.5k; R_0402_1005Metric
R8: 10.2k; R_0603_1608Metric
R9: 1.91k; R_0603_1608Metric
R10, R11: 10k; R_0402_1005Metric
SW1, SW2: TS-1187A-B-A-B; SW_Push_1P1T_NO_CK_KSC6xxJ
U1: ADR5040ARTZ-2.048; SOT-23
U2: LM393; SOIC127P600X175-8N
U3: TPS54331D; SOIC-8-1EP_3.9x4.9mm_P1.27mm_EP2.29x3mm_ThermalVias
U4: LP3993-33B3F; SOT-23
U5: RFM95W-915S2; HOPERF_RFM9XW_SMD
U6: USBLC6-2SC6; SOT-23-6
U7: STM32F411RETx; LQFP-64_10x10mm_P0.5mm
U8: BMX055
Y1: 32.768k; Crystal_SMD_3215-2Pin_3.2x1.5mm
Y2: 12MHz; Crystal_SMD_5032-4Pin_5.0x3.2mm

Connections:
+3.3V: C4.1, C5.1, C16.1, J1.4 (VDD), U4.2 (VOUT), U5.13 (3.3V)
+3V3: C9.1, C10.1, C22.1, C23.1, C24.1, C25.1, J5.1, L2.1, R11.2, SW1.2, U7.1 (VBAT), U7.19 (VDD), U7.32 (VDD), U7.48 (VDD), U7.64 (VDD), U8.3 (VDD), U8.13 (VDDIO)
+5V: C6.1, C13.1, C19.1, D3.1 (K), J6.2, J7.2, L1.2, R8.2, U4.3 (VIN)
/CE_ACC: U7.26 (PB0), U8.16 (CSB1)
/CE_GYR: U7.27 (PB1), U8.5 (CSB2)
/CE_MAG: U7.28 (PB2), U8.20 (CSB3)
/CLK_SD: J1.5 (CLX), U7.51 (PC10)
/CS_RF: U5.5 (NSS), U7.10 (PC2)
/CS_SD: J1.2 (CD/DAT3), J1.9 (CD), U7.11 (PC3)
/IMU_MISO: U7.22 (PA6), U8.12 (SDO2), U8.17 (SDO1)
/IMU_MOSI: U7.23 (PA7), U8.11 (SDX)
/IMU_SCK: U7.21 (PA5), U8.9 (SCX)
/MISO_RF: U5.2 (MISO), U7.35 (PB14)
/MISO_SD: J1.7 (DAT0), U7.52 (PC11)
/MOSI_RF: U5.3 (MOSI), U7.36 (PB15)
/MOSI_SD: J1.3 (CMD), U7.53 (PC12)
/RESET_RF: U5.6 (RESET), U7.9 (PC1)
/RF_1O0: U5.14 (DIO0), U7.8 (PC0)
/SCK_RF: U5.4 (SCK), U7.34 (PB13)
/STM32/BOOT0: R10.2, SW1.1, U7.60 (BOOT0)
/STM32/NRST: C20.1, R11.1, SW2.2, U7.7 (NRST)
/STM32/OSC32_IN: C1.1, U7.3 (PC14), Y1.1
/STM32/OSC32_OUT: C2.1, U7.4 (PC15), Y1.2
/STM32/OSC_IN: C21.1, U7.5 (PH0), Y2.1
/STM32/OSC_OUT: C3.1, U7.6 (PH1), Y2.3
/STM32/S1_control: J6.1, U7.56 (PB4)
/STM32/S1_feedback: J6.4, U7.16 (PA2)
/STM32/S2_control: J7.1, U7.57 (PB5)
/STM32/S2_feedback: J7.4, U7.17 (PA3)
/STM32/SWCLK: J5.4, U7.49 (PA14)
/STM32/SWDIO: J5.3, U7.46 (PA13)
/STM32/USB_D+: U6.6 (I/O1), U7.45 (PA12)
/STM32/USB_D-: U6.4 (I/O2), U7.44 (PA11)
/STM32/USB_conn_D+: J4.3 (D+), U6.1 (I/O1)
/STM32/USB_conn_D-: J4.2 (D-), U6.3 (I/O2)
GND: C1.2, C2.2, C3.2, C4.2, C5.2, C6.2, C7.2, C9.2, C10.2, C11.2, C12.2, C13.2, C14.2, C15.2, C16.2, C17.2, C18.2, C19.2, C20.2, C21.2, C22.2, C23.2, C24.2, C25.2, C26.2, D2.2 (A), J1.6 (VSS), J1.MP1, J1.MP2, J1.MP3, J1.MP4, J2.2, J3.2 (Ext), J4.5 (GND), J4.6 (Shield), J5.2, J6.3, J7.3, R2.1, R4.1, R9.1, R10.1, SW2.1, U1.2 (A), U2.4 (V-), U3.7 (GND), U4.1 (GND), U5.1 (GND), U5.8 (GND), U5.10 (GND), U6.2 (GND), U7.12 (VSSA), U7.18 (VSS), U7.31 (VSS), U7.47 (VSS), U7.63 (VSS), U8.4 (GNDA), U8.6 (GNDIO), U8.7 (PS), Y2.2, Y2.4
unnamed: C17.1, R7.1
unnamed: D1.2 (A), Q1.1 (G), R2.2
unnamed: C8.2, D2.1 (K), L1.1, U3.8 (PH)
unnamed: J2.1, Q1.3 (D)
unnamed: J3.1 (In), U5.9 (ANT)
unnamed: Q2.1 (G), R5.1, U2.1
unnamed: R1.1, U1.1 (K), U2.3 (+)
unnamed: R3.1, R4.2, U2.2 (-)
unnamed: C8.1, U3.1 (BOOT)
unnamed: C18.1, R7.2, U3.6 (COMP)
unnamed: R6.1, U3.3 (EN)
unnamed: C15.1, U3.4 (SS)
unnamed: R8.1, R9.2, U3.5 (VSENSE)
unnamed: C26.1, U7.30 (VCAP1)
unnamed: C11.1, L2.2, U7.13 (VDDA)
VBUS: D3.2 (A), J4.1 (VBUS), U6.5 (VBUS)
VCC: C12.1, C14.1, Q2.3 (D), R6.2, U3.2 (VIN)
VDC: C7.1, D1.1 (K), Q1.2 (S), Q2.2 (S), R1.2, R3.2, R5.2, U2.8 (V+)

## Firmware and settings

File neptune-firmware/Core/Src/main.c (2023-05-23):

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
/* Includes ------------------------------------------------------------------*/
#include "main.h"
#include "cmsis_os.h"
#include "usb_device.h"

/* USER CODE BEGIN Includes */
#include <math.h>
#include <string.h>
#include "usbd_cdc_if.h"
#include "arm_math.h"

#include "BMX055.h"
#include "LoRa.h"
#include "Sensors.h"
#include "packets.h"
#include "EKF.h"
#include "utils.h"
#include "servos.h"

// #include "arm_math.h"
// #include "usbd_cdc_if.h"
// #include "string.h"
// #include "BMX055.h"
// #include "Sensors.h"
// #include "utils.h"
// #include "packets.h"
// #include "LoRa.h"
// #include "servos.h"
// #include "EKF.h"

// #include <stdbool.h>
// #include <math.h>
// #include "usbd_cdc_if.h"
// #include "arm_math.h"

// #include "BMX055.h"
// #include "MS5611.h"
// #include "LoRa.h"
// #include "Sensors.h"
// #include "Packets.h"
// #include "EKF.h"
// #include "debug.h"
// #include "gps.h"
// #include "State_Machine.h"
/* USER CODE END Includes */

/* USER CODE BEGIN PTD */
#define SAMPLE_FREQUENCY 100
#define ACCEL_ALPHA 0.9
#define GYRO_ALPHA 0.5
/* USER CODE END PTD */

/* USER CODE BEGIN PD */
float32_t hard_iron_offset_data[3] = { 46.5, 74.0, -44.0 };
float32_t soft_iron_offset_data[9] = { 1, 0, 0, 0, 1, 0, 0, 0, 1 };
/* USER CODE END PD */

ADC_HandleTypeDef hadc1;

SPI_HandleTypeDef hspi1;
SPI_HandleTypeDef hspi2;
SPI_HandleTypeDef hspi3;

TIM_HandleTypeDef htim2;
TIM_HandleTypeDef htim3;

/* Definitions for SensorRead */
osThreadId_t SensorReadHandle;
const osThreadAttr_t SensorRead_attributes = {
  .name = "SensorRead",
  .stack_size = 512 * 4,
  .priority = (osPriority_t) osPriorityRealtime,
};
/* Definitions for LoRa */
osThreadId_t LoRaHandle;
const osThreadAttr_t LoRa_attributes = {
  .name = "LoRa",
  .stack_size = 512 * 4,
  .priority = (osPriority_t) osPriorityLow7,
};
/* Definitions for ServoActuate */
osThreadId_t ServoActuateHandle;
const osThreadAttr_t ServoActuate_attributes = {
  .name = "ServoActuate",
  .stack_size = 512 * 4,
  .priority = (osPriority_t) osPriorityRealtime,
};
/* Definitions for KalmanFilter */
osThreadId_t KalmanFilterHandle;
const osThreadAttr_t KalmanFilter_attributes = {
  .name = "KalmanFilter",
  .stack_size = 1024 * 4,
  .priority = (osPriority_t) osPriorityRealtime,
};
/* USER CODE BEGIN PV */
int SERVO_ENABLED = 0;  // disabled by default
/* USER CODE END PV */

void SystemClock_Config(void);
static void MX_GPIO_Init(void);
static void MX_SPI1_Init(void);
static void MX_SPI2_Init(void);
static void MX_SPI3_Init(void);
static void MX_ADC1_Init(void);
static void MX_TIM3_Init(void);
static void MX_TIM2_Init(void);
void start_sensor_reading(void *argument);
void start_LoRa_task(void *argument);
void start_servo_control(void *argument);
void start_kalman_filter(void *argument);

/* USER CODE BEGIN PFP */
BMX055_Handle bmx055;
BMX055_Data_Handle bmx055_data;
Motors motors;
TIM_HandleTypeDef *Micros_Timer = &htim2;

/* Define data class structs */
int trace_counter = 0;
BMX055_Handle bmx055;
BMX055_Data_Handle bmx055_data;
LoRa LoRa_Handle;
EKF ekf;
float EKF_K[12] = { 0, 0, 0, 0, 0, 0, 0, 0, 0, 0, 0, 0 };
float qu[4] = { 1, 0, 0, 0 }; // Corresponds to 0, 0, 0 YPR
float EKF_P[16] = { 0.01, 0, 0, 0, 0, 0.01, 0, 0, 0, 0, 0.01, 0, 0, 0, 0, 0.01 };
float EKF_Q[16] = { 0.01, 0, 0, 0, 0, 0.01, 0, 0, 0, 0, 0.01, 0, 0, 0, 0, 0.01 };
float EKF_R[9] = { 496, 025, 271, 025, 379, 326, 271, 326, 998 }; // These are in units of 100*m/s^2
/* USER CODE END PFP */

/* USER CODE BEGIN 0 */
uint32_t micros(TIM_HandleTypeDef *timer) {
	return __HAL_TIM_GET_COUNTER(timer);
}

void HAL_GPIO_EXTI_Callback(uint16_t GPIO_Pin) {
	// Give notification to Sample_Sensors_Handle so that scheduler enables the task
//	vTaskNotifyGiveFromISR(Sample_Sensors_Handle, NULL);
	switch (GPIO_Pin) {
	// case GPIO_PIN_4:
	// 	/* Accelerometer interrupt */
	// 	// Log time of interrupt
	// 	bmx055_data.accel[4] = bmx055_data.accel[3];
	// 	bmx055_data.accel[3] = micros(Micros_Timer);
	// 	xTaskNotifyFromISR(SensorReadHandle, (uint32_t)Accel_Sensor, eSetBits, NULL);
	// 	return;
	// case GPIO_PIN_5:
	// 	/* Gyroscope interrupt */
	// 	// Log time of interrupt
	// 	bmx055_data.gyro[4] = bmx055_data.gyro[3];
	// 	bmx055_data.gyro[3] = micros(Micros_Timer);
	// 	xTaskNotifyFromISR(SensorReadHandle, (uint32_t)Gyro_Sensor, eSetBits, NULL);
	// 	return;
	// case GPIO_PIN_6:
	// 	/* Magnetometer interrupt */
	// 	// Log time of interrupt
	// 	bmx055_data.mag[4] = bmx055_data.mag[3];
	// 	bmx055_data.mag[3] = micros(Micros_Timer);
	// 	xTaskNotifyFromISR(SensorReadHandle, (uint32_t)Mag_Sensor, eSetBits, NULL);
	// 	return;
	case GPIO_PIN_0:
		/* LoRa interrupt */
		xTaskNotifyFromISR(LoRaHandle, NULL, eNoAction, NULL);
	default:
		return;
	}
}
/* USER CODE END 0 */

/**
  * @brief  The application entry point.
  * @retval int
  */
int main(void)
{
  /* MCU Configuration--------------------------------------------------------*/

  /* Reset of all peripherals, Initializes the Flash interface and the Systick. */
  HAL_Init();

  /* Configure the system clock */
  SystemClock_Config();

  /* Initialize all configured peripherals */
  MX_GPIO_Init();
  MX_SPI1_Init();
  MX_SPI2_Init();
  MX_SPI3_Init();
  MX_ADC1_Init();
  MX_TIM3_Init();
  MX_TIM2_Init();
  /* USER CODE BEGIN 2 */
  HAL_NVIC_DisableIRQ(EXTI0_IRQn);
  HAL_TIM_PWM_Start(&htim3, TIM_CHANNEL_1);
  HAL_TIM_PWM_Start(&htim3, TIM_CHANNEL_2);

  /* LoRa configurations */
	LoRa_Handle = newLoRa();
	LoRa_Handle.hSPIx = &hspi2;
	LoRa_Handle.CS_port = RF_CE_GPIO_Port;
	LoRa_Handle.CS_pin = RF_CE_Pin;
	LoRa_Handle.reset_port = RF_RESET_GPIO_Port;
	LoRa_Handle.reset_pin = RF_RESET_Pin;
	LoRa_Handle.DIO0_port = RF_10O_GPIO_Port;
	LoRa_Handle.DIO0_pin = RF_10O_Pin;

	LoRa_Handle.frequency = 915;
	LoRa_Handle.spredingFactor = SF_7;						// default = SF_7
	LoRa_Handle.bandWidth = BW_125KHz;				  	// default = BW_125KHz
	LoRa_Handle.crcRate = CR_4_5;						// default = CR_4_5
	LoRa_Handle.power = POWER_20db;					// default = 20db
	LoRa_Handle.overCurrentProtection = 120; 				// default = 100 mA
	LoRa_Handle.preamble = 8;		  					// default = 8;

	HAL_GPIO_WritePin(RF_CE_GPIO_Port, RF_CE_Pin, GPIO_PIN_SET);

  /* Assign magnetometer calibration constants */
	arm_mat_init_f32(&bmx055.mag_hard_iron_offsets, 3, 1, hard_iron_offset_data);
	arm_mat_init_f32(&bmx055.mag_soft_iron_offsets, 3, 3, soft_iron_offset_data);

  /* BMX055 configurations */
	bmx055.hspi = &hspi1;
	// Accelerometer parameters
	bmx055.acc_CS_port = ACC_CE_GPIO_Port;
	bmx055.acc_CS_pin = ACC_CE_Pin;
	bmx055.acc_range = BMX055_ACC_RANGE_4;
	bmx055.acc_bandwidth = BMX055_ACC_PMU_BW_7_81;

	// Gyroscope parameters
	bmx055.gyro_CS_port = GYR_CE_GPIO_Port;
	bmx055.gyro_CS_pin = GYR_CE_Pin;
	bmx055.gyro_range = BMX055_GYRO_RANGE_65_6;		// 500 deg/s
	bmx055.gyro_bandwidth = BMX055_GYRO_BW_64;

	// Magnetometer parameters
	bmx055.mag_CS_port = MAG_CE_GPIO_Port;
	bmx055.mag_CS_pin = MAG_CE_Pin;
	bmx055.mag_data_rate = BMX055_MAG_DATA_RATE_30;

  /* Servo configurations */

	/* Start timers */
	HAL_TIM_Base_Start(Micros_Timer);

  /* USER CODE END 2 */

  /* Init scheduler */
  osKernelInitialize();

  /* USER CODE BEGIN RTOS_MUTEX */
  /* add mutexes, ... */
  /* USER CODE END RTOS_MUTEX */

  /* USER CODE BEGIN RTOS_SEMAPHORES */
  /* add semaphores, ... */
  /* USER CODE END RTOS_SEMAPHORES */

  /* USER CODE BEGIN RTOS_TIMERS */
  /* start timers, add new ones, ... */
  /* USER CODE END RTOS_TIMERS */

  /* USER CODE BEGIN RTOS_QUEUES */
  /* add queues, ... */
  /* USER CODE END RTOS_QUEUES */

  /* Create the thread(s) */
  /* creation of SensorRead */
  SensorReadHandle = osThreadNew(start_sensor_reading, NULL, &SensorRead_attributes);

  /* creation of LoRa */
  LoRaHandle = osThreadNew(start_LoRa_task, NULL, &LoRa_attributes);

  /* creation of ServoActuate */
  ServoActuateHandle = osThreadNew(start_servo_control, NULL, &ServoActuate_attributes);

  /* creation of KalmanFilter */
  // KalmanFilterHandle = osThreadNew(start_kalman_filter, NULL, &KalmanFilter_attributes);

  /* USER CODE BEGIN RTOS_THREADS */
  /* add threads, ... */
  /* USER CODE END RTOS_THREADS */

  /* USER CODE BEGIN RTOS_EVENTS */
  /* add events, ... */
  /* USER CODE END RTOS_EVENTS */

  /* Start scheduler */
  osKernelStart();

  /* We should never get here as control is now taken by the scheduler */
  /* Infinite loop */
  /* USER CODE BEGIN WHILE */
  while (1)
  {
    /* USER CODE END WHILE */

    /* USER CODE BEGIN 3 */


//  	float accel_data[3];
//	  BMX055_readAccel(&bmx055, accel_data);
//
//    float roll;
//    float pitch;
//
//    get_roll_and_pitch(accel_data, &roll, &pitch);
//
//    char str_buff[50];
//    sprintf(str_buff, "Roll: %.2f\tPitch: %.2f\r\n", roll, pitch);
//   	CDC_Transmit_FS(str_buff, strlen(str_buff));
//


	// 5% duty cycle minimum, 10% maximum
	// 16 bit, 65536 increments

	// arr = 200, duty cycle = ccr / arr * 100
	// if (duty_cycle > 11) {
	// 	reverse = 1;
	// 	duty_cycle = 11-3.5;
	// } else if (duty_cycle < 4) {
	// 	reverse = 0;
	// 	duty_cycle = 4+3.5;
	// }

//	 sprintf(str_buff, "Cycle: %.1f%%\r\n", duty_cycle);
//	 CDC_Transmit_FS(str_buff, strlen(str_buff));

	// htim3.Instance->CCR1 = duty_cycle * 200 / 100;
	// htim3.Instance->CCR2 = duty_cycle * 200 / 100;

	// if (reverse) {
	// 	duty_cycle -= 3.5;
	// } else {
	// 	duty_cycle += 3.5;
	// }




	// HAL_Delay(50);
  }
  /* USER CODE END 3 */
}

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
/* USER CODE BEGIN Header_start_sensor_reading */
/**
  * @brief  Function implementing the SensorRead thread.
  * @param  argument: Not used
  * @retval None
  */
/* USER CODE END Header_start_sensor_reading */
void start_sensor_reading(void *argument)
{
  /* init code for USB_DEVICE */
  MX_USB_DEVICE_Init();
  /* USER CODE BEGIN 5 */
	// Init BMX055
	if (!BMX055_init(&bmx055)) {
		printf("[main] BMX055 failed to start\r\n");
	}
  // We're not using interrupts (good idea for V2 though)
	// BMX055_setInterrupts(&bmx055);

	uint8_t data;

	/* GPS config */
//  gps_init_tpv(&tpv);
//	GNSS_Init(&GNSS_Handle, GPS_UART);
//	GNSS_LoadConfig(&GNSS_Handle);
	/* EXTI interrupt init*/
//	HAL_NVIC_SetPriority(EXTI4_IRQn, 5, 0);
	// HAL_NVIC_EnableIRQ(EXTI4_IRQn);

//	HAL_NVIC_SetPriority(EXTI9_5_IRQn, 5, 0);
	// HAL_NVIC_EnableIRQ(EXTI9_5_IRQn);

//	HAL_NVIC_SetPriority(EXTI15_10_IRQn, 5, 0);
	// HAL_NVIC_EnableIRQ(EXTI15_10_IRQn);

	// Sensor type that is ready when task is released
	uint32_t sensor_type;
  osDelay(2000);  // give it a lil
	/* Infinite loop */
	for (;;) {
		// Wait for sensors to be ready before running task
		// xTaskNotifyWait(0, 0, &sensor_type, (TickType_t) portMAX_DELAY);

		/* Check each sensor each loop for new data */
    float accel_data[3];
    float gyro_data[3];
    BMX055_readAccel(&bmx055, accel_data);
    BMX055_exp_filter(bmx055_data.accel, accel_data, bmx055_data.accel, sizeof(accel_data) / sizeof(int),
    ACCEL_ALPHA);
    BMX055_readGyro(&bmx055, gyro_data);
    BMX055_exp_filter(bmx055_data.gyro, gyro_data, bmx055_data.gyro, sizeof(gyro_data) / sizeof(int),
    GYRO_ALPHA);
    BMX055_readCompensatedMag(&bmx055, bmx055_data.mag);

    osDelay(10);  // every 30ms let's grab some new data
	}
  /* USER CODE END 5 */
}

/* USER CODE BEGIN Header_start_LoRa_task */
/**
* @brief Function implementing the LoRa thread.
* @param argument: Not used
* @retval None
*/
/* USER CODE END Header_start_LoRa_task */
void start_LoRa_task(void *argument)
{
  /* USER CODE BEGIN start_LoRa_task */
	HAL_NVIC_EnableIRQ(EXTI0_IRQn);
  LoRa_reset(&LoRa_Handle);
	LoRa_setModulation(&LoRa_Handle, LORA_MODULATION);
	if (LoRa_init(&LoRa_Handle) != LORA_OK) {
      CDC_Transmit_FS("LoRa connection failed\r\n", strlen("LoRa connection failed\r\n"));
	}

	LoRa_startReceiving(&LoRa_Handle);

//  for (;;) { // testing if we receive anything
//	int amount = LoRa_received_bytes(&LoRa_Handle);
//    if (amount) {
//        uint8_t read_data[255];
//        size_t bytes_read = LoRa_receive(&LoRa_Handle, read_data, sizeof(read_data));
//
//        for (int i=0; i < bytes_read; i++) {
//        	uint8_t var = read_data[i];
//        }
//        // uint8_t resp = 1;
//        // LoRa_transmit(&LoRa_Handle, &resp, 1, TRANSMIT_TIMEOUT);
//    }
//
//  }
  /* Infinite loop */
  for(;;)
  {
    // Wait for LoRa to be ready before running task
    xTaskNotifyWait(0, 0, NULL, (TickType_t) portMAX_DELAY);

    // Read bytes in FIFO buffer
    uint8_t read_data[255];
    size_t bytes_read = LoRa_receive(&LoRa_Handle, read_data, sizeof(read_data));
    switch (read_data[0]) {
      case SET_ANGLES: ;
      	if (bytes_read < 3) break;
//      	SERVO_ENABLED = 1;
//      	motors.m1_angle = (float) read_data[1];
//      	motors.m2_angle = (float) read_data[2];
      	set_motor(1, 1, (float) read_data[bytes_read-2], htim3);
      	set_motor(2, 1, (float) read_data[bytes_read-1], htim3);
        break;
      case GIMBLE_MOTORS:
        gimble_test(htim3);
        break;
      case PONG: ;
        uint8_t resp = 1;
        LoRa_transmit(&LoRa_Handle, &resp, 1, TRANSMIT_TIMEOUT);
        break;
      case SENS_REPORT: ;
        float dummy[2];
        get_roll_and_pitch(bmx055_data.accel, &dummy[0], &dummy[1]);
        uint8_t packet[4];
        if (dummy[0] < 0) {
        	packet[0] = 1;  // sign bit
        	packet[1] = round(-dummy[0]);
        } else {
        	packet[0] = 0;  // sign bit
        	packet[1] = round(dummy[0]);
        }
        if (dummy[1] < 0) {
        	packet[2] = 1;  // sign bit
        	packet[3] = round(-dummy[1]);
        } else {
        	packet[2] = 0;  // sign bit
        	packet[3] = round(dummy[1]);
        }

        LoRa_transmit(&LoRa_Handle, &packet[0], 1, TRANSMIT_TIMEOUT);
        LoRa_transmit(&LoRa_Handle, &packet[1], 1, TRANSMIT_TIMEOUT);
        LoRa_transmit(&LoRa_Handle, &packet[2], 1, TRANSMIT_TIMEOUT);
        LoRa_transmit(&LoRa_Handle, &packet[3], 1, TRANSMIT_TIMEOUT);
//        LoRa_transmit(&LoRa_Handle, packet, 4, TRANSMIT_TIMEOUT);
        break;
      case COUNTER_TILT: ;
        SERVO_ENABLED = !SERVO_ENABLED;
      default:
        break;
    }
  }
  /* USER CODE END start_LoRa_task */
}

/* USER CODE BEGIN Header_start_servo_control */
/**
* @brief Function implementing the ServoActuate thread.
* @param argument: Not used
* @retval None
*/
/* USER CODE END Header_start_servo_control */
void start_servo_control(void *argument)
{
  /* USER CODE BEGIN start_servo_control */
  /* Infinite loop */
  for(;;)
  {
    if (SERVO_ENABLED) {
      // roll increases == servo decreases
      // pitch increases == servo decreases
        float roll;
        float pitch;
        get_roll_and_pitch(bmx055_data.accel, &roll, &pitch);
        pitch = fmaxf(fminf((90 - pitch*1.15), 170), 10);
        roll = fmaxf(fminf(90 - (roll - 90)*1.15, 170), 10);
        set_motor(1, 0, roll, htim3);
      	set_motor(2, 0, pitch, htim3);
    }
    osDelay(30);
  }
  /* USER CODE END start_servo_control */
}

/* USER CODE BEGIN Header_start_kalman_filter */
/**
* @brief Function implementing the KalmanFilter thread.
* @param argument: Not used
* @retval None
*/
/* USER CODE END Header_start_kalman_filter */
void start_kalman_filter(void *argument)
{
  /* USER CODE BEGIN start_kalman_filter */
	uint32_t currentSampleTime = 0;
	uint32_t lastSampleTime = 0;
	int correct_freq = 1;
	int idx = 0;
	EKF_Init(&ekf, qu, EKF_K, EKF_P, EKF_Q, EKF_R, 0.0);
	float fake_acc_dat[10][3] = { { 0, 0, -9.81 }, { 1.703, 0, 9.66 }, { 3.355, 0, 9.218 }, { 4.905, 0, 8.496 }, { 6.306, 0, 7.515 }, { 7.515, 0, 6.306 }, { 8.496, 0, 4.905 }, { 9.218, 0, 3.355 }, { 9.66, 0, 1.703 }, { -9.81, 0, 0 } };
	float fake_gyr_dat[10][3] = { { 0, 0.175, 0 }, { 0, 0.175, 0 }, { 0, 0.175, 0 }, { 0, 0.175, 0 }, { 0, 0.175, 0 }, { 0, 0.175, 0 }, { 0, 0.175, 0 }, { 0, 0.175, 0 }, { 0, 0.175, 0 }, { 0, 0.175, 0 } };
//	osDelay(3000);

	/* Infinite loop */
	for (;;) {
		trace_counter++;
		currentSampleTime = micros(Micros_Timer);
		float dt = (currentSampleTime - lastSampleTime) / 1E6;
		lastSampleTime = currentSampleTime;

		float p = (float) (bmx055_data.gyro[0]);
		float q = (float) (bmx055_data.gyro[1]);
		float r = (float) (bmx055_data.gyro[2]);
		EKF_Predict(&ekf, p, q, r, dt);
		if (idx % correct_freq == 0) {
			EKF_Update(&ekf, (float) bmx055_data.accel[0] / 100, (float) bmx055_data.accel[1] / 100, (float) bmx055_data.accel[2] / 100, 1.5, 0, 0);
			idx = 0;
		}
		idx++;
		float euler_result[3];
		EP2Euler321(ekf.qu_data, euler_result);
		char printData[256];
		size_t sz;
		// Print pqr rates in rad/s
//		sz = snprintf(printData, sizeof(printData), "%0.6f, %0.6f, %0.6f, %0.6f\r\n", p, q, r, dt);
//		debug_print(printData, sz);
		// Print Euler angles
//		sz = snprintf(printData, sizeof(printData), "roll:%0.2f pitch:%0.2f yaw:%0.2f\r\n",
//				euler_result[0] * 57.2958, euler_result[1] * 57.2958,
//				euler_result[2] * 57.2958);
//		debug_print(printData, sz);
		// Print quaternions
//	sz = snprintf(printData, sizeof(printData), "%0.10f, %0.10f, %0.10f, %0.10f, %0.10f, %0.10f, %0.10f, %0.10f, %0.10f, %0.10f, %0.10f\r\n", p, q, r, dt, ekf.qu_data[0],
//				ekf.qu_data[1], ekf.qu_data[2], ekf.qu_data[3], euler_result[0], euler_result[1], euler_result[2]);
//		debug_print(printData, sz);
//		sz = snprintf(printData, sizeof(printData), "Orientation: %0.4f, %0.4f, %0.4f\r\n", euler_result[0] * 57.2958, euler_result[1] * 57.2958, euler_result[2] * 57.2958);
//		debug_print(printData, sz, dbg=DBG);
		osDelay(30);
//		for (int idx = 0; idx < 10; idx++) {
//			EKF_Predict(&ekf, fake_gyr_dat[idx][0], fake_gyr_dat[idx][1], fake_gyr_dat[idx][2], 1.0);
//			EKF_Update(&ekf, fake_acc_dat[idx][0], fake_acc_dat[idx][1], fake_acc_dat[idx][2], 1.5, 0, 0);
//
//			float euler_result[3];
//			EP2Euler123(ekf.qu_data, euler_result);
//			char printData[128];
//			size_t sz = snprintf(printData, sizeof(printData), "%0.2f, %0.2f, %0.2f\r\n", euler_result[0] * 57.2958,
//					euler_result[1] * 57.2958, euler_result[2] * 57.2958);
//			debug_print(printData, sz);
//			osDelay(1000);
//		}
	}
  /* USER CODE END start_kalman_filter */
}

/**
  * @brief  This function is executed in case of error occurrence.
  * @retval None
  */
void Error_Handler(void)
{
  /* USER CODE BEGIN Error_Handler_Debug */
  /* User can add his own implementation to report the HAL error return state */
  __disable_irq();
  while (1)
  {
  }
  /* USER CODE END Error_Handler_Debug */
}

#ifdef  USE_FULL_ASSERT
/**
  * @brief  Reports the name of the source file and the source line number
  *         where the assert_param error has occurred.
  * @param  file: pointer to the source file name
  * @param  line: assert_param error line source number
  * @retval None
  */
void assert_failed(uint8_t *file, uint32_t line)
{
  /* USER CODE BEGIN 6 */
  /* User can add his own implementation to report the file name and line number,
     ex: printf("Wrong parameters value: file %s on line %d\r\n", file, line) */
  /* USER CODE END 6 */
}
#endif /* USE_FULL_ASSERT */

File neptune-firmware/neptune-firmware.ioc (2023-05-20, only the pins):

Mcu.UserName=STM32F411RETx
PA11.Signal=USB_OTG_FS_DM
PA12.Signal=USB_OTG_FS_DP
PA13.Signal=SYS_JTMS-SWDIO
PA14.Signal=SYS_JTCK-SWCLK
PA2.GPIO_Label=S1_FBK
PA2.Signal=ADCx_IN2
PA3.GPIO_Label=S2_FBK
PA3.Signal=ADCx_IN3
PA5.GPIO_Label=IMU_SCK
PA5.Signal=SPI1_SCK
PA6.GPIO_Label=IMU_MISO
PA6.Signal=SPI1_MISO
PA7.GPIO_Label=IMU_MOSI
PA7.Signal=SPI1_MOSI
PB0.GPIO_Label=ACC_CE
PB0.Signal=GPIO_Output
PB1.GPIO_Label=GYR_CE
PB1.Signal=GPIO_Output
PB13.GPIO_Label=RF_SCK
PB13.Signal=SPI2_SCK
PB14.GPIO_Label=RF_MISO
PB14.Signal=SPI2_MISO
PB15.GPIO_Label=RF_MOSI
PB15.Signal=SPI2_MOSI
PB2.GPIO_Label=MAG_CE
PB2.Signal=GPIO_Output
PB4.GPIO_Label=S1_CTRL
PB4.Signal=S_TIM3_CH1
PB5.GPIO_Label=S2_CTRL
PB5.Signal=S_TIM3_CH2
PC0.GPIO_Label=RF_10O
PC0.Signal=GPXTI0
PC1.GPIO_Label=RF_RESET
PC1.Signal=GPIO_Output
PC10.GPIO_Label=SD_SCK
PC10.Signal=SPI3_SCK
PC11.GPIO_Label=SD_MISO
PC11.Signal=SPI3_MISO
PC12.GPIO_Label=SD_MOSI
PC12.Signal=SPI3_MOSI
PC14-OSC32_IN.Signal=RCC_OSC32_IN
PC15-OSC32_OUT.Signal=RCC_OSC32_OUT
PC2.GPIO_Label=RF_CE
PC2.Signal=GPIO_Output
PC3.GPIO_Label=SD_CE
PC3.Signal=GPIO_Output

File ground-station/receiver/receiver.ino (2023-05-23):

#include <SPI.h>
#include <LoRa.h>
byte readByte;
int counter = 0;
void setup() {
  Serial.begin(115200);
  while (!Serial);
  while (!LoRa.begin(915E6)) {
    // Serial.write(0xFA);
    ;
  }
  LoRa.enableCrc();
}


void loop() {
  // try to parse packet
  int packetSize = LoRa.parsePacket();
  if (packetSize) {
    // read packet
    for (int i = 0; i < packetSize; i++) {
      Serial.write(LoRa.read());
    }
  }

  // LoRa.beginPacket();
  // LoRa.write(counter);
  // LoRa.endPacket();
  // delay(10000);
  // counter++;
  if (Serial.available() > 0) {
    int indicator = Serial.read();
    if (indicator == 27) {
      Serial.write(0x66);
      return;
    } else {
      // if (indicator == 1) {
      //   char buff[100];
      //   unsigned long x = Serial.read() << 24;
      //   x = x | Serial.read() << 16;
      //   x = x | Serial.read() << 8;
      //   x = x | Serial.read();
      //   unsigned long y = Serial.read() << 24;
      //   y = y | Serial.read() << 16;
      //   y = y | Serial.read() << 8;
      //   y = y | Serial.read();
      //   sprintf(buff, "X: %d\tY: %d", x, y);

      //   while (Serial.available());
      //   Serial.println(buff);
      //   return;
      // }
      size_t packet_length = 1;
      uint8_t packet[1024];
      packet[0] = indicator;
      while (Serial.available()) {
        // Read data into buffer
        readByte = Serial.read();
        packet[packet_length] = readByte;
        packet_length++;
      }

      // Transmit buffer
      LoRa.beginPacket();
      LoRa.write(packet, packet_length);
      LoRa.endPacket();
      LoRa.receive();
    }
  }

// Used to test receive and transmit
//  if (millis() % 1000) {
//    uint8_t packet[] = {0x04, 0xa7, 0xab, 0x00, 0xd4 };
//    LoRa.beginPacket();
//    LoRa.write(packet, sizeof(packet));
//    LoRa.endPacket(false);
//    LoRa.receive();
//  }
}



    // size_t packet_length = 0;
    // uint8_t packet[1024];

    // if (indicator == 1) {
      // float angle_x = Serial.read() << 24;
      // angle_x = ((unsigned long) angle_x) | (Serial.Read() << 16);
      // angle_x = ((unsigned long) angle_x) | (Serial.Read() << 8);
      // angle_x = ((unsigned long) angle_x) | Serial.Read();

    //   float angle_y = Serial.read() << 24;
    //   angle_y = ((unsigned long) angle_y) | (Serial.Read() << 16);
    //   angle_y = ((unsigned long) angle_y) | (Serial.Read() << 8);
    //   angle_y = ((unsigned long) angle_y) | Serial.Read();
    // } else if (indicator == 2) {

    // }

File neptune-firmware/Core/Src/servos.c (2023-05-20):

/*
 * servos.c
 *
 *  Created on: 12 May 2023
 *      Author: jb
 */

#include "servos.h"

float _degrees_to_duty_cycle(float degrees) {
	float duty_cycle = MIN_DUTY_CYCLE + ((MAX_DUTY_CYCLE - MIN_DUTY_CYCLE) / (MAX_ANGLE - MIN_ANGLE)) * (degrees - MIN_ANGLE);

	return duty_cycle;
}

float _byte_to_duty_cycle(float byte) {
	float duty_cycle = MIN_DUTY_CYCLE + ((MAX_DUTY_CYCLE - MIN_DUTY_CYCLE) / 255) * byte;

	return duty_cycle;
}

void set_motor(int motor_id, int mode, float input, TIM_HandleTypeDef htim) {
	float duty_cycle;
	if (mode == 0) {
		duty_cycle = _degrees_to_duty_cycle(input);
	} else {
		duty_cycle = _byte_to_duty_cycle(input);
	}

	// duty cycle = ccr / arr * 100
	float normalised = duty_cycle * 200 / 100;

	if (motor_id == 1) {
		htim.Instance->CCR1 = normalised;
	} else if (motor_id == 2) {
		htim.Instance->CCR2 = normalised;
	} else {
		// log an error over USB
		char buff[50];
		sprintf(buff, "ERROR: Invalid motor ID: %d\n", motor_id);
		CDC_Transmit_FS(buff, strlen(buff));
	}
}

void gimble_test(TIM_HandleTypeDef htim) {
	set_motor(1, 0, 0, htim);
	HAL_Delay(1000);
	set_motor(1, 0, 180, htim);
	HAL_Delay(1000);
	set_motor(1, 0, 90, htim);
	HAL_Delay(1000);
	set_motor(2, 0, 0, htim);
	HAL_Delay(1000);
	set_motor(2, 0, 180, htim);
	HAL_Delay(1000);
	set_motor(2, 0, 90, htim);
	HAL_Delay(1000);

	for (int angle=0; angle < 180; angle++) {
		set_motor(1, 0, angle, htim);
		set_motor(2, 0, angle, htim);
		HAL_Delay(10);
	}
}
// we have our min, max, and need to normalise that to 0 to 180

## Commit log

2023-04-22 Added power regulation circuity
    [RF.kicad_sch, haste.kicad_pcb, haste.kicad_sch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]
2023-04-23 Renamed to Neptune
    [RF.kicad_sch, neptune.kicad_pcb, neptune.kicad_sch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]
2023-04-23 Continued work on board
    [STM32.kicad_sch, Sensors.kicad_sch, data_management.kicad_sch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]
2023-04-24 Added oscillator, setup sensor SPI
    [STM32.kicad_sch, Sensors.kicad_sch, data_management.kicad_sch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]
2023-04-24 Continued pcb work
    [STM32.kicad_sch, Sensors.kicad_sch, data_management.kicad_sch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]
2023-04-24 Schematic done I think
    [STM32.kicad_sch, Sensors.kicad_sch, data_management.kicad_sch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]
2023-04-25 PCB done, pending review
    [STM32.kicad_sch, Sensors.kicad_sch, data_management.kicad_sch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]
2023-04-26 Added mounting holes
    [neptune.kicad_pcb, neptune.kicad_sch]
2023-04-26 Created production files
    [neptune-B_Cu.gbr, neptune-B_Mask.gbr, neptune-B_Paste.gbr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]
2023-04-27 Generated BOM
    [neptune.csv]
2023-05-01 Final PCB changes
    [neptune-B_Cu.gbr, neptune-B_Mask.gbr, neptune-B_Paste.gbr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]
2023-05-08 Finished STM32 setup
2023-05-09 Setting up firmware
    [neptune.kicad_pcb]
2023-05-09 Made basic servo test code
2023-05-14 Working on sensor code
2023-05-15 Roll and pitch calculations in progress
2023-05-17 Sensor reading success
2023-05-17 Finally, sensor reading works
2023-05-19 Ready for some initial testing
    [neptune-B_Cu.gbr, neptune-B_Mask.gbr, neptune-B_Paste.gbr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]
2023-05-20 Slight changes to try debug issues
    [ground_station.py, main.c, neptune-firmware.ioc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]
2023-05-20 Preparing to switch to polling setup
2023-05-20 Preliminary working model ready to debug jitter issues
    [main.c, main.h, neptune-firmware.ioc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]
2023-05-20 Ground station updated
2023-05-20 Merging main
    [STM32.kicad_sch, Sensors.kicad_sch, data_management.kicad_sch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]
2023-05-21 Ready to test sensors
2023-05-21 Ground station updates
2023-05-23 Fixed corrupt PCB file, updated schematic
    [STM32.kicad_sch, Sensors.kicad_sch, data_management.kicad_sch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]
2023-05-24 Added CAD files
    [0.5_inch_female.SLDPRT, 0.5_inch_male.SLDPRT, 100mm_pipe.SLDDRW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]
2023-06-21 Rolled back flight computer to before corrupted
    [STM32.kicad_sch, Sensors.kicad_sch, data_management.kicad_sch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]

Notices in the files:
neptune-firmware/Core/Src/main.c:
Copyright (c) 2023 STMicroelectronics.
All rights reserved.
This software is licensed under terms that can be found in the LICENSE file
